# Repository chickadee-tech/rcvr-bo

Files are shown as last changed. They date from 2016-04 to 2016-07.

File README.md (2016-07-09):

# Chickadee Tech Receiver Breakout Polystack Mod #
This is a breakout board designed for connecting a variety of Remote Control receivers to the control board. It supports Serial RX, PPM and PPM along with telemetry.

## Documentation ##
See the [wiki](https://github.com/chickadee-tech/rcvr-bo/wiki) for documentation.

## Polystack ##
This **mod** board is part of the Polystack platform for modular microcontrol systems. More information on the platform can be found at [polystack.org](http://polystack.org).

## Support ##
If you need support with a board you own or have development questions please email support@chickadee.tech or check [chickadee.tech/support](https://chickadee.tech/support) for other ways to get support.

## Contributing ##
Please note that this project is released with a [Contributor Code of Conduct](CODE_OF_CONDUCT.md). By participating in this project you agree to abide by its terms.

### Setup ###
Components and footprints for PCB parts are not included in this repository. Instead, checkout the [chickadee-tech/kicad-libs](https://github.com/chickadee-tech/kicad-libs) repository in the same directory that this repository is checked out in. All part definitions should be relative so that they will load correctly.

### Pull requests ###
For fixes please submit a pull request to the original repository. After the pull request is merged, check the [Chickadee Tech Active Contributor Discount (ACD)](https://chickadee.tech/active-contributor) to see if you are eligible for a discount code to use on your next purchase.

### Derivatives ###
If developing your own version of the Receiver Breakout board please remove all Chickadee Tech trademarks and follow the [CC-BY license](LICENSE). While not required, please consider open sourcing your modifications so others can learn from your improvements. If you do email support@chickadee.tech and we may choose to add your project to the ACD.

You may also license the Polystack logo for free by emailing support@chickadee.tech. We'll ask for your gerbers to ensure the design complies with specifications laid out [here](https://github.com/chickadee-tech/polystack/wiki) and provide written permission to use the trademark after compliance has been demonstrated.

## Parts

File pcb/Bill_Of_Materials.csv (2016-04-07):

part name | symbol | size (imp) | max current | unit price | units per build | units in stock | order total | Manufacturer ID | source url | datasheet | datasheet2
80 pin header | PORT_IN1 |  |  | $1.35 | 1 | 1 | $1.35 | DF40C-80DP-0.4V(51) | http://www.digikey.com/product-detail/en/DF40C-80DP-0.4V(51)/H11632CT-ND/1969511 | N | http://www.hirose.co.jp/cataloge_hp/ed_DF40_20140305.pdf |  | Total Base Cost | $12.32
80 pin receptacle (3.0mm) | PORT_OUT1 |  |  | $2.76 | 1 | 3 | $2.76 | DF40HC(3.0)-80DS-0.4V(51) | http://www.digikey.com/product-detail/en/DF40HC(3.0)-80DS-0.4V(58)/H124954CT-ND/5399048 | N |  | price ranges 1.40 - 2.50
AND/OR gate | PORT_ANDOR1 |  |  | $0.25 | 1 | 2 | $0.25 | SN74LVC1G0832DCKR | http://www.digikey.com/product-detail/en/SN74LVC1G0832DCKR/296-18754-1-ND/863884 |  | http://www.ti.com/lit/ds/symlink/sn74lvc1g0832.pdf
multifunction gate | PORT_XOR1, PORT_INV1 |  |  | $0.14 | 2 | 6 | $0.28 | SN74LVC1G58DCKR | http://www.digikey.com/product-detail/en/SN74LVC1G58DCKR/296-15577-1-ND/571153 |  | http://www.ti.com/lit/ds/symlink/sn74lvc1g58.pdf
64kbit eeprom | PORT_IC1 | udfn |  | $0.61 | 1 | 2 | $0.61 | AT24CS64-MAHM-T | http://www.digikey.com/product-detail/en/AT24CS64-MAHM-T/AT24CS64-MAHM-TCT-ND/4292118 | N | http://www.atmel.com/images/atmel-8870-seeprom-at24cs64-datasheet.pdf
R 10k | PORT_R1 | 603 |  | $0.01 | 1 | 979 | $0.01 | RC0603FR-0710KL | http://www.digikey.com/product-detail/en/RC0603FR-0710KL/311-10.0KHRCT-ND/729827 | MF-RES-0603-10K | http://www.yageo.com/NewPortal/yageodocoutput?fileName=/pdf/R-Chip/PYu-RC_Group_51_RoHS_L_3.pdf
C 0.1uF | PORT_C1 | 603 |  | $0.02 | 1 | 400 | $0.02 | C0603C104K4RACTU | http://www.digikey.com/product-detail/en/C0603C104K4RACTU/399-1096-1-ND/411371 | MF-CAP-0603-0.1uF | http://www.kemet.com/docfinder?Partnumber=C0603C104K4RACTU
C 1uF X7R | C1 | 603 |  | $0.03 | 1 | 20 | $0.03 | TMK107B7105KA-T | http://www.digikey.com/product-detail/en/TMK107B7105KA-T/587-2984-1-ND/2714177 | MF-CAP-0603-1uF | http://ds.yuden.co.jp/TYCOMPAS/ut/detail.do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
C 10uF X5R | C2 | 1206 |  | $0.24 | 1 | 80 | $0.24 | C3216X5R1C106M160AA | http://www.digikey.com/product-detail/en/C3216X5R1C106M160AA/445-1426-1-ND/569092 | MF-CAP-1206-10uF | http://product.tdk.com/en/catalog/datasheets/mlcc_commercial_general_en.pdf
green led | D2 |  |  | $0.19 | 1 | 83 | $0.19 | LTST-C190KGKT | http://www.digikey.com/product-detail/en/LTST-C190KGKT/160-1435-1-ND/386814 | Y | http://optoelectronics.liteon.com/upload/download/DS22-2000-074/S_110_LTST-C190KGKT.pdf
yellow led | D3 |  |  | $0.20 | 1 | 87 | $0.20 | LTST-C190KSKT | http://www.digikey.com/product-detail/en/LTST-C190KSKT/160-1437-1-ND/386818 | N | http://optoelectronics.liteon.com/upload/download/DS-22-99-0189/S_110_LTST-C190KSKT.pdf
red led | D4 |  |  | $0.19 | 1 | 71 | $0.19 | LTST-C190KRKT | http://www.digikey.com/product-detail/en/LTST-C190KRKT/160-1436-1-ND/386816 | MF-LED-0603-RED | http://optoelectronics.liteon.com/upload/download/DS-22-99-0151/S_110_LTST-C190KRKT.pdf
n-channel mosfet | Q1 | TO-236-3, SC-59, SOT-23-3 | 220mA continuous | $0.09 | 1 | 59 | $0.09 | BSS138 | http://www.digikey.com/product-detail/en/BSS138/BSS138CT-ND/244294 | MF-DSC-SOT233-BSS138 | https://www.fairchildsemi.com/datasheets/BS/BSS138.pdf
R 10k | R1, R5 | 603 |  | $0.01 | 2 | 979 | $0.02 | RC0603FR-0710KL | http://www.digikey.com/product-detail/en/RC0603FR-0710KL/311-10.0KHRCT-ND/729827 | MF-RES-0603-10K | http://www.yageo.com/NewPortal/yageodocoutput?fileName=/pdf/R-Chip/PYu-RC_Group_51_RoHS_L_3.pdf
R 1k | R2, R3, R4 | 603 |  | $0.01 | 3 | 993 | $0.03 | RC0603FR-071KL | http://www.digikey.com/product-detail/en/RC0603FR-071KL/311-1.00KHRCT-ND/729790 | MF-RES-0603-1K | http://www.yageo.com/NewPortal/yageodocoutput?fileName=/pdf/R-Chip/PYu-RC_Group_51_RoHS_L_3.pdf
4 XOR | U1 | 14-VQFN |  | $0.39 | 1 | 6 | $0.39 | SN74AHC86RGYR | http://www.digikey.com/product-detail/en/SN74AHC86RGYR/296-13905-1-ND/521431 | N | http://www.ti.com/lit/ds/symlink/sn74ahc86.pdf
Dual Three State Buffer | U2 | 8-TSSOP | 8ma | $0.38 | 1 | 0 | $0.38 | 74AHC2G125DP,125 | http://www.digikey.com/product-detail/en/nxp-semiconductors/74AHC2G125DP,125/568-8794-1-ND/2813712 | N | http://www.nxp.com/documents/data_sheet/74AHC_AHCT2G125.pdf
3.3v regulator | U3 | SOT23-5 | 0.3A | $0.49 | 1 | 8 | $0.49 | TLV70233DBVR | http://www.digikey.com/product-detail/en/TLV70233DBVR/296-32415-1-ND/3505572 | MF-REG-SOT235-3.3V-300mA | http://www.ti.com/lit/ds/symlink/tlv702.pdf
Octal Buffer | U4 | tssop20 |  | $0.36 | 1 | 9 | $0.36 | SN74LVC244APWR | http://www.digikey.com/product-detail/en/SN74LVC244APWR/296-1230-1-ND/276498 | N | http://www.ti.com/lit/ds/symlink/sn74lvc244a.pdf
Receiver Breakout v1 | PCB |  |  | $3.37 | 1 | 3 | $3.37 | CKD-RBO-V1 |  | N
3mm Spacer | Off Board |  |  | $0.05 | 5 | 100 | $0.25 | 908-3MM | http://www.mouser.com/ProductDetail/Bivar/908-3MM/ | N | http://www.bivar.com/Portals/0/Products/d.ashx?f=/Portals/0/products/9XX-XXX.pdf
1x2 right angle tin straight | Off Board |  |  | $0.21 | 1 | 4 | $0.21 | 22-28-8020 | http://www.digikey.com/product-search/en?keywords=22-28-8020 | N
1x12 right angle | Off Board |  |  | $0.61 | 1 | 0 | $0.61 | 22-28-8120 |  | N

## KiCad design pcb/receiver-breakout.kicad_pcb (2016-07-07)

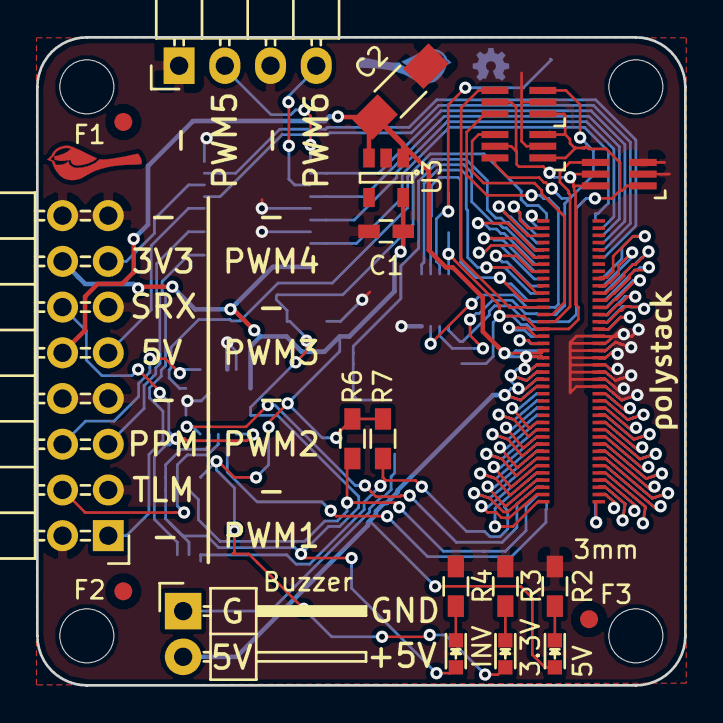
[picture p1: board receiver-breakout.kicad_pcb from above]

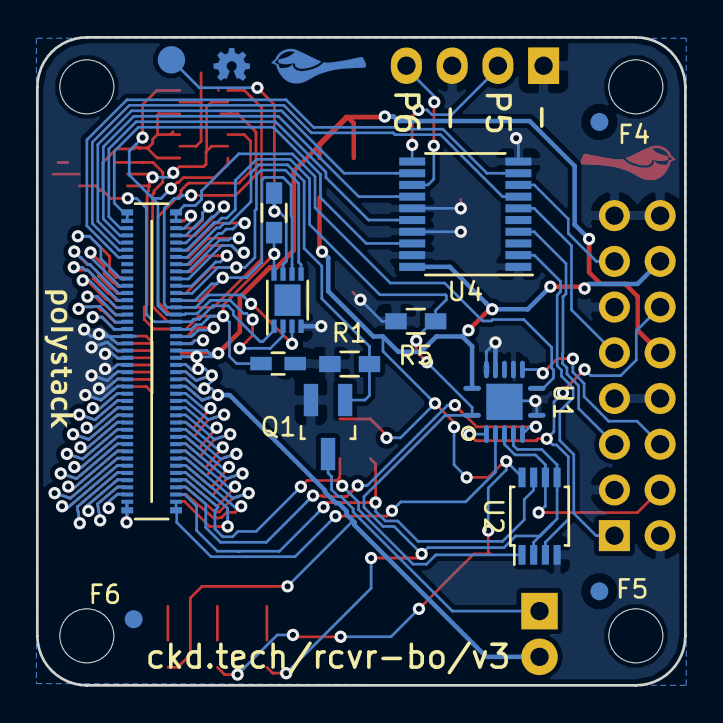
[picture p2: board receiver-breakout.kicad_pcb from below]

Board: 2 copper layers, 36.0 x 36.0 mm, 37 parts (15 on the bottom side), 84 nets.

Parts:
C1: 1uF; C_0603_HandSoldering
C2: 10uF; C_1206_HandSoldering
D2: Green; LED_0603
D3: Yellow; LED_0603
D4: Red; LED_0603
F1, F2, F3, F4, F5, F6: 1mm; Fiducial
P1: CONN_02X08; Pin_Header_Angled_2x08
P2: CONN_01X02; Pin_Header_Angled_1x02
P3: CONN_01X04; Pin_Header_Angled_1x04
PORT_ANDOR1: SN74LVC1G0832; SC-70-6_Handsoldering
PORT_C1: 0.1uF; C_0603_HandSoldering
PORT_IC1: AT24CS02-MAHM; DFN-8-1EP_3x2mm_Pitch0.5mm
PORT_IN1: CKD_SANDWICH; DF40-80pin-Header
PORT_INV1: SN74LVC1G58; SC-70-6_Handsoldering
PORT_OUT1: CKD_SANDWICH; DF40-3-4mm-80pin-Receptacle
PORT_P1: CONN_01X01; Measurement_Point_Round-SMD-Pad_Small
PORT_R1: 10k; R_0603_HandSoldering
PORT_XOR1: SN74LVC1G58; SC-70-6_Handsoldering
Q1: Q_NMOS_GSD; SOT-23_Handsoldering
R1, R5, R6, R7: 10K; R_0603_HandSoldering
R2, R3, R4: 1k; R_0603_HandSoldering
U1: 74LS86; QFN-14-3.5x3.5mm
U2: 74AHC2G125; TSSOP-8_3x3mm_Pitch0.65mm
U3: TLV70233DBV; SOT-23-5
U4: 74LS244; TSSOP-20_4.4x6.5mm_Pitch0.65mm
svg2mod, svg2mod#2: G***; polystack-bold-0.4

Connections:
+5V: C2.1, D2.2, P1.10, P2.2, PORT_IN1.19, PORT_IN1.20, PORT_IN1.21, PORT_IN1.22, PORT_IN1.23, PORT_IN1.24, PORT_OUT1.19, PORT_OUT1.20, PORT_OUT1.21, PORT_OUT1.22, PORT_OUT1.23, PORT_OUT1.24, U3.1, U3.3
/ExpansionPort/3V3_0.3A_E: PORT_IN1.17, PORT_OUT1.17
/ExpansionPort/3V3_0.3A_LL: PORT_ANDOR1.5, PORT_C1.1, PORT_IC1.8, PORT_IN1.16, PORT_INV1.5, PORT_INV1.6, PORT_OUT1.16, PORT_R1.2, PORT_XOR1.5
/ExpansionPort/+BATT: PORT_IN1.18, PORT_OUT1.18
/ExpansionPort/ADC1: PORT_IN1.49, PORT_OUT1.49
/ExpansionPort/ADC2: PORT_IN1.50, PORT_OUT1.50
/ExpansionPort/BOOT: PORT_IN1.65, PORT_OUT1.65
/ExpansionPort/CAN_HI: PORT_IN1.67, PORT_OUT1.67
/ExpansionPort/CAN_LO: PORT_IN1.68, PORT_OUT1.68
/ExpansionPort/GPIO1: D4.2, PORT_IN1.5, R5.1, U1.1, U1.5, U2.2, U2.5
/ExpansionPort/GPIO2: PORT_IN1.6, Q1.1, R1.1
/ExpansionPort/GPIO3: PORT_IN1.7, PORT_OUT1.5
/ExpansionPort/GPIO4: PORT_IN1.8, PORT_OUT1.6
/ExpansionPort/GPIO5: PORT_IN1.9, PORT_OUT1.7
/ExpansionPort/GPIO6: PORT_IN1.10, PORT_OUT1.8
/ExpansionPort/HEIGHT_1: PORT_ANDOR1.1, PORT_IC1.1, PORT_IN1.15, PORT_INV1.1, PORT_XOR1.1, PORT_XOR1.3
/ExpansionPort/HEIGHT_2: PORT_ANDOR1.3, PORT_IC1.2, PORT_IN1.14, PORT_XOR1.6
/ExpansionPort/HEIGHT_4: PORT_ANDOR1.6, PORT_IC1.3, PORT_IN1.13
/ExpansionPort/NEW_HEIGHT_1: PORT_INV1.4, PORT_OUT1.15
/ExpansionPort/NEW_HEIGHT_2: PORT_OUT1.14, PORT_XOR1.4
/ExpansionPort/NEW_HEIGHT_4: PORT_ANDOR1.4, PORT_OUT1.13
/ExpansionPort/RESET: PORT_IN1.66, PORT_OUT1.66
/ExpansionPort/SDMMC1_CK: PORT_IN1.55, PORT_OUT1.55
/ExpansionPort/SDMMC1_CMD: PORT_IN1.56, PORT_OUT1.56
/ExpansionPort/SDMMC1_D0: PORT_IN1.51, PORT_OUT1.51
/ExpansionPort/SDMMC1_D1: PORT_IN1.52, PORT_OUT1.52
/ExpansionPort/SDMMC1_D2: PORT_IN1.53, PORT_OUT1.53
/ExpansionPort/SDMMC1_D3: PORT_IN1.54, PORT_OUT1.54
/ExpansionPort/SPI1_MISO: PORT_IN1.79, PORT_OUT1.79
/ExpansionPort/SPI1_MOSI: PORT_IN1.80, PORT_OUT1.80
/ExpansionPort/SPI1_NSS: PORT_IN1.77, PORT_OUT1.77
/ExpansionPort/SPI1_SCK: PORT_IN1.78, PORT_OUT1.78
/ExpansionPort/SPI2_MISO: PORT_IN1.75, PORT_OUT1.75
/ExpansionPort/SPI2_MOSI: PORT_IN1.76, PORT_OUT1.76
/ExpansionPort/SPI2_NSS: PORT_IN1.73, PORT_OUT1.73
/ExpansionPort/SPI2_SCK: PORT_IN1.74, PORT_OUT1.74
/ExpansionPort/SPI3_MISO: PORT_IN1.71, PORT_OUT1.71
/ExpansionPort/SPI3_MOSI: PORT_IN1.72, PORT_OUT1.72
/ExpansionPort/SPI3_NSS: PORT_IN1.69, PORT_OUT1.69
/ExpansionPort/SPI3_SCK: PORT_IN1.70, PORT_OUT1.70
/ExpansionPort/TIM1: PORT_IN1.1, U1.8
/ExpansionPort/TIM2: PORT_IN1.2, PORT_OUT1.1
/ExpansionPort/TIM3: PORT_IN1.3, PORT_OUT1.2
/ExpansionPort/TIM4: PORT_IN1.4, PORT_OUT1.3
/ExpansionPort/TIMG1_CH1: PORT_IN1.41, U4.18
/ExpansionPort/TIMG1_CH2: PORT_IN1.42, U4.16
/ExpansionPort/TIMG1_CH3: PORT_IN1.43, U4.14
/ExpansionPort/TIMG1_CH4: PORT_IN1.44, U4.12
/ExpansionPort/TIMG2_CH1: PORT_IN1.45, U4.7
/ExpansionPort/TIMG2_CH2: PORT_IN1.46, U4.9
/ExpansionPort/UART1_RX: PORT_IN1.40, U1.3
/ExpansionPort/UART1_TX: PORT_IN1.39, R6.2, U2.7
/ExpansionPort/UART2_RX: PORT_IN1.38, U1.6
/ExpansionPort/UART2_TX: PORT_IN1.37, R7.2, U2.1
/ExpansionPort/UART3_RX: PORT_IN1.36, PORT_OUT1.40
/ExpansionPort/UART3_TX: PORT_IN1.35, PORT_OUT1.39
/ExpansionPort/UART4_RX: PORT_IN1.34, PORT_OUT1.38
/ExpansionPort/UART4_TX: PORT_IN1.33, PORT_OUT1.37
/ExpansionPort/UART5_RX: PORT_IN1.32, PORT_OUT1.36
/ExpansionPort/UART5_TX: PORT_IN1.31, PORT_OUT1.35
/ExpansionPort/UART6_RX: PORT_IN1.30, PORT_OUT1.34
/ExpansionPort/UART6_TX: PORT_IN1.29, PORT_OUT1.33
/ExpansionPort/UART7_RX: PORT_IN1.28, PORT_OUT1.32
/ExpansionPort/UART7_TX: PORT_IN1.27, PORT_OUT1.31
/ExpansionPort/UART8_RX: PORT_IN1.26, PORT_OUT1.30
/ExpansionPort/UART8_TX: PORT_IN1.25, PORT_OUT1.29
/ExpansionPort/i2c_SCL: PORT_IC1.6, PORT_IN1.12, PORT_OUT1.12
/ExpansionPort/i2c_SDA: PORT_IC1.5, PORT_IN1.11, PORT_OUT1.11
/PPM: P1.6, U1.9
/PWM1: P1.1, U4.2
/PWM2: P1.5, U4.4
/PWM3: P1.9, U4.6
/PWM4: P1.13, U4.8
/PWM5: P3.2, U4.11
/PWM6: P3.4, U4.13
/RC: P1.12, U1.2, U2.3
/TELEM: P1.4, U1.4, U2.6
GND: C1.2, C2.2, P1.2, P1.3, P1.7, P1.8, P1.11, P1.15, P1.16, P3.1, P3.3, PORT_ANDOR1.2, PORT_C1.2, PORT_IC1.4, PORT_IN1.57, PORT_IN1.58, PORT_IN1.59, PORT_IN1.60, PORT_IN1.61, PORT_IN1.62, PORT_IN1.63, PORT_IN1.64, PORT_INV1.2, PORT_INV1.3, PORT_OUT1.57, PORT_OUT1.58, PORT_OUT1.59, PORT_OUT1.60, PORT_OUT1.61, PORT_OUT1.62, PORT_OUT1.63, PORT_OUT1.64, PORT_XOR1.2, Q1.2, R1.2, R2.2, R3.2, R4.2, R5.2, U1.7, U1.10, U1.12, U1.13, U2.4, U3.2, U4.1, U4.10, U4.15, U4.17, U4.19
unnamed: D2.1, R2.1
unnamed: D3.1, R3.1
unnamed: D4.1, R4.1
unnamed: P2.1, Q1.3
unnamed: PORT_IC1.7, PORT_P1.1, PORT_R1.1
VCC: C1.1, D3.2, P1.14, R6.1, R7.1, U1.14, U2.8, U3.5, U4.20

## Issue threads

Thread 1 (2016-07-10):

Use p-channel mosfet to control LL voltage.

tannewt, 2016-07-10:
The 3V3_LL voltage is on when on USB and leaks out through the XORs and Buffers. Add a mosfet that stops it when main voltage isn't present.

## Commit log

2016-02-07 Initial work on receiver breakout to support receivers without cradles.
    [ExpansionPort.sch, receiver-breakout.kicad_pcb, receiver-breakout.sch]
2016-03-05 Receiver Breakout v1 which should support all receivers that Cleanflight does.
    [Bill_Of_Materials.csv, ExpansionPort.sch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]
2016-04-07 Unknown changes to receiver breakout.
    [Bill_Of_Materials.csv, ExpansionPort.sch, receiver-breakout.kicad_pcb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]
2016-04-13 Rebrand everything to Polystack and increment versions.
    [receiver-breakout.kicad_pcb]
2016-04-16 Final gerbers for test manufacturing run.
    [receiver-breakout-B.Cu.gbl, receiver-breakout-B.Mask.gbs, receiver-breakout-B.Paste.gbp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]
2016-06-07 Update polystack logo to bold variant, connect i2c lines to eeprom and bump version number.
    [ExpansionPort.sch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]
2016-07-07 Add license information to many files. PCB design files are CC-BY and code is MIT license.
    [ExpansionPort.sch, receiver-breakout.kicad_pcb, receiver-breakout.sch]
2016-07-07 Convert to relative component and footprint paths.
    [ExpansionPort.sch, receiver-breakout.sch]

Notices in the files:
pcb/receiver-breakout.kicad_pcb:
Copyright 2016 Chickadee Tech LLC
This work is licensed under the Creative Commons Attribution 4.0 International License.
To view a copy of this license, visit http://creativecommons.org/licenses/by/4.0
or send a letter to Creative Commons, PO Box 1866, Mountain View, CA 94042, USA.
